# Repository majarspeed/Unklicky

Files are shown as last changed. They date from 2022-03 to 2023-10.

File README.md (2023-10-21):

# Thank you Guys 
I love seeing the makes and all the questions and some awesome derivates are coming out of this project. 

And there is an amazing Euclid derivitive doen by Minisekt you can view [Unclid here](https://github.com/Minsekt/unclid).

There are new versions of the unklicky for the KlickyNG, JosAr has integrated the unklicky concept into the NG or next generations of Klicky. Check it out here https://github.com/jlas1/Klicky-Probe/tree/main/Probes

A great tutorial on Klicky/Unklicky was made by a member of the discord if you have any questions this should help for the setup. Thanks Logan BC 🇨🇦 VT.435 for creating such a great resouce. https://github.com/LoganFraser/VoronMods/tree/main/KlickySetup

# Unklicky

Drop in magnet based klicky probe In the orginal and now a 6x3 magnet variant called the BFP. 

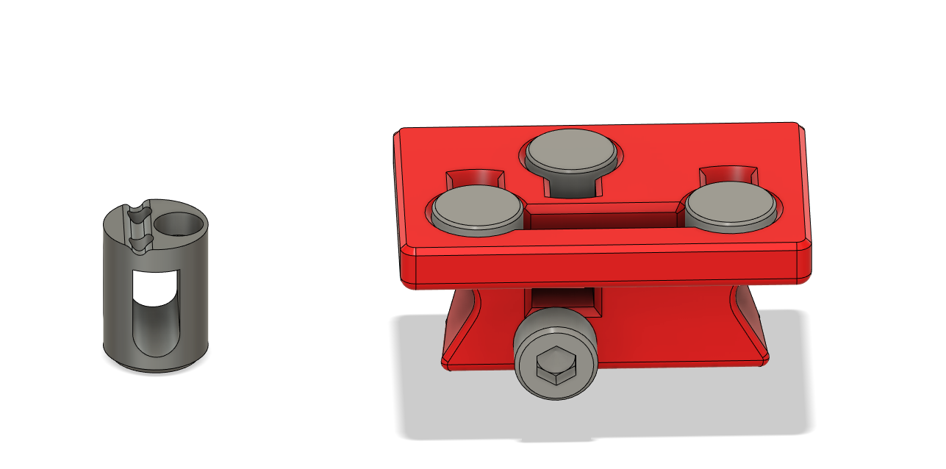
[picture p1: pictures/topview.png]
Top

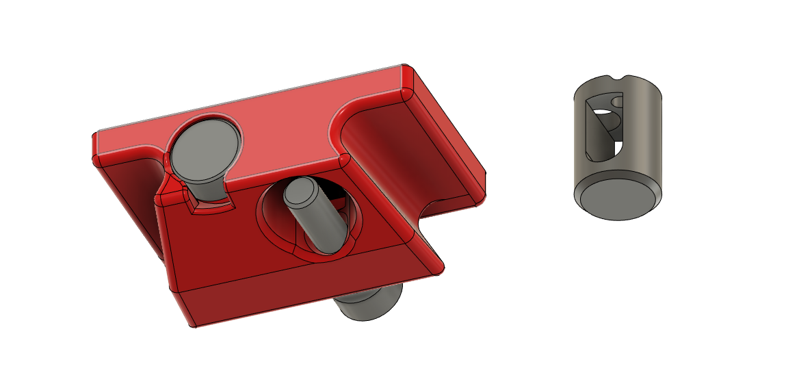
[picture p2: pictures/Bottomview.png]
Botton Bottom


Also keep in mind that klicky is based off the original work done over at Annex Engineering the excellent work that was done with the quickdraw probe. 
Thanks for calling this out. I did know the original was based on their work but it slipped my mind. They have an excellent group that does a lot of good things for the community. Support them in there work and thanks for keeping me honest here guys. 
https://github.com/Annex-Engineering/Quickdraw_Probe

Klicky is also based on [Euclid](https://www.euclidprobe.com/).

Thanks go to JosAR again for all the hard work and testing, please support his project and all the hard work he has done and is continuing to do. 
https://github.com/jlas1/Klicky-Probe

Testing with the auto z
While the switch offset can be changed by wire thickness on the wrap. 6mm seems to be a safe starting point for the the unklicky. And 3.2 seems to be a good starting point for the BFP. You can mesure from the body to the probe point to get the switch offset. And visit Protoloft and support him for all the work he has done on the auto z project. https://github.com/protoloft/klipper_z_calibration 

Parts kits thanks to DFH

[Buy full kit here](https://deepfriedhero.in/products/unklicky-full-kit-by-dustinspeed?_pos=1&_psq=unkl&_ss=e&_v=1.0&aff=8 "Full Unklicky Kit")

[Buy sidegrade kit here](https://deepfriedhero.in/products/unklicky-sidegrade-kit-by-dustinspeed?_pos=2&_sid=d0a66cc6e&_ss=r&aff=8 "Sidegrade Unklicky Kit")

# Unklicky TAP

This is a unklicky sensor for TAP. Thanks to the Voron team for this design and Badnoob for spearheading the effort and lead developer role.

It's almost as precise as the optical sensor, it's main goal is to reduce the initial Voron hug (a lot of people start buying the same obscure part, leaving it out of stock). With that said i can see one using it as a primary sensor as it can achieve a range in probing better than 0.0025 with a standard deviation of 0.001.

**A range of 0.001 is excellent and enough for our 3D printer needs.** don't chase unicorns.

It's pretty easy to install, it does require a somewhat tuned printer.

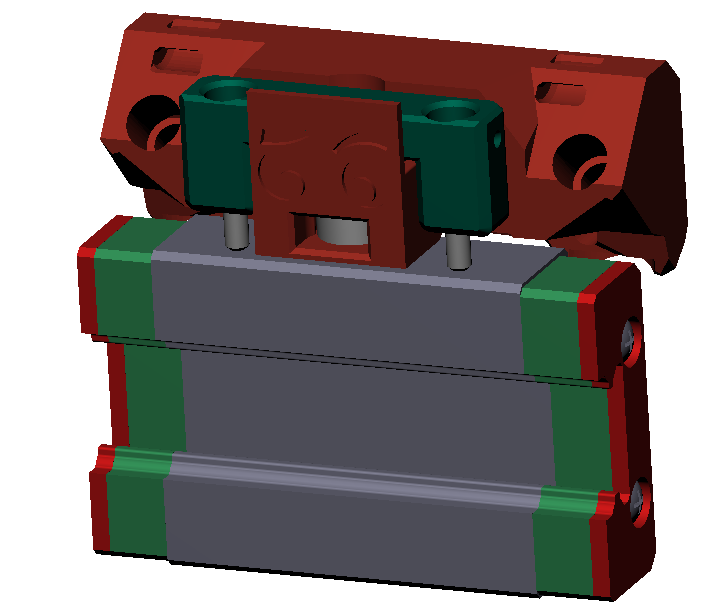
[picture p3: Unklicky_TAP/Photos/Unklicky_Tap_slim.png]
Unklicky TAP
|  |
| :----------------------------------------------------------: |

# How does it work?

The principle behind this sensor, is using the MGN12 steel carriage to make contact with two m2x10 self tapping screws, thereby closing the circuit between the mcu GND (or V-) and the probe (should use a endstop) signal pin.
Two 6x3 magnets makes the pin attract the probe body.

## More information

More information [here](./Unklicky_TAP)

## Versions and differences 

| Unklicky TAP | usage |
| --- | --- |
| ~~Unklicky TAP~~ | ~~It's almost a drop in replacement/spare for the optical PCB for TAP, it uses the same footprint, is installed on the same TAP upper part, but only requires 2 cables, a mcu GND (or V-) and the probe (should use a endstop) signal pin, it does not need a 5v connection.<br />Requires Umbilical cables to the toolhead~~<br />Discontinued, the released TAP upper part is too large, screws don't touch on the MGN12 carriage |
| [Unklicky TAP](./Unklicky_TAP) | It's embedded in it's own TAP upper part (due to space constrains between TAP and the cable chains), but only requires 2 cables, a mcu GND (or V-) and the probe (should use a endstop) signal pin, it does not need a 5v or 24v connection.<br />Previously called UnklickyTAP slim, renamed when the larger sibling was discontinued |

| Unklicky Probes | usage |
| --- | --- |
| [Unklicky](./Unklicky_Probes/Unklicky) | The original. Made to retain the same shape and body as klicky. It uses 3x2 magnets in the pin. Uses wire wrapped pin method |
| [Unklicky BFP](./Unklicky_Probes/BFP) | Larger body to allow the use of a 6 x 3 standard magnet. Uses the original wire wrapped pin method |
| [Unklicky BFP-HS](./Unklicky_Probes/BFP-HS) | Even Larger body to allow the use of a 6 x 3 standard magnet and a heatset in the pin to allow a shorter pin throw. And more clearance for wires. Does not increase accuracy but does make the build easier. |
| [Unklicky BFP for v0/Tiny-M](https://github.com/jlas1/Klicky-Probe/tree/main/Probes/Unklicky) | Larger body to allow the use of a 6 x 3 standard magnet, pivot arm version to reduce inaccessible bed space. Uses the original wire wrapped pin method |
| [UnklickyNG](https://github.com/jlas1/Klicky-Probe/tree/main/Probes/UnklickyNG) | Original Unklicky mod compatible with [KlickyNG](https://github.com/jlas1/Klicky-Probe/tree/main/Probes#klickyng) mounts. It uses 3x2 magnets in the pin. Uses wire wrapped pin method |
| [UnklickyNG BFP](https://github.com/jlas1/Klicky-Probe/tree/main/Probes/UnklickyNG) | Original Unklicky BFP mod compatible with [KlickyNG](https://github.com/jlas1/Klicky-Probe/tree/main/Probes#klickyng) mounts. Larger body to allow the use of a 6 x 3 standard magnet. Uses the original wire wrapped pin method |
| [Unclid](https://github.com/Minsekt/unclid) | Unclid Probe ([Euclid](https://www.euclidprobe.com/) probe replacement), uses two screws and the magnet to close the switch circuit |
| [Sidewipe Unklicky](https://github.com/chestwood96/SlideSwipe/tree/master/Experimental/UnklickySlideSwipe(better%20name%20pending)) | Sidewipe Unklicky by chestwood96, This is a bit of a mixture of unklicky and mechabl in a SlideswipeProbe formfactor.  |

| Unklicky Endstops | usage |
| --- | --- |
| [Unklicky Z](./Unklicky_Endstops/Unklicky_z) | First standard z endstop has multiple pin options. Uses the Heat set pin method and was intended to be modular and allow for customization of the pins |
| [Unklicky Sexbolt](./Unklicky_Endstops/Unklicky_SexBolt) | Sex bolt mod. Uses a single pin and 5mm OD chicago screw or sexbolt and 695/f695 bearing. |
| [Unklicky Sexbolt-SBS (bearing sleeve)](./Unklicky_Endstops/Unklicky_SexBolt) | Sex bolt mod. Uses a single pin and 5mm OD chicago screw or sexbolt. Allows the reuse of bearing sleeve from other sexbolt mods. |
| [Unklicky Sexbolt Bearing free version](./Unklicky_Endstops/Unklicky_SexBolt) | Sex bolt mod. Uses a single pin and 6mm OD and 5mm rod with a chicago screw or sexbolt. |
| [Parametric Sexbolt unklicky Z](https://github.com/PorcoMaster/SexPillar) | Parametric Sex bolt + Unklicky mod. (from PorcoMaster) |

| Other Unklicky inspired designs | usage |
| --- | --- |
| [RunoutUnklicky](https://github.com/waytotheweb/voron/tree/main/general/RunoutUnklicky) | The Runout UnKlicky Sensor is a filament runout sensor that can be used to pause a print if printing filament breaks, runs out or otherwise is no longer present in the sensor.The design uses magnets as the switch, making it easy and cheap to source BOM components. |

# Unklicky Newest version 2
New version of the 3x2 probe is now available. This includes some QOL improvements. But does not really improve on any performance in any significant way. 
Added a screw mount on the rear so a magnet or screw can be used. May be useful if you have especially strong magnets.
Added a shaped pin that is easier to wire. And only inserts in one direction. 
New pin can be printed flat on the plate to make it easier to print and align the layer lines for smoother operation. 
V1 will be retained for now as well.

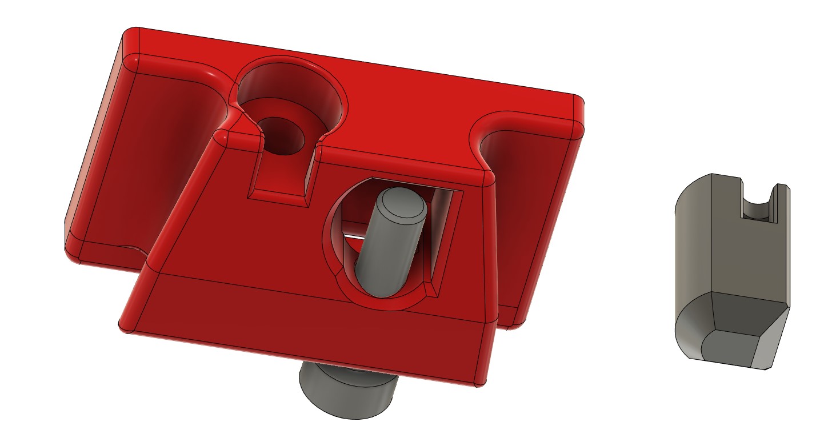
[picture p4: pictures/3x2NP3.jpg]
V2 3x2


# BFP newest Version 6

This is a 6x3 unklicky probe, it's a mod developed by me and JosAr.
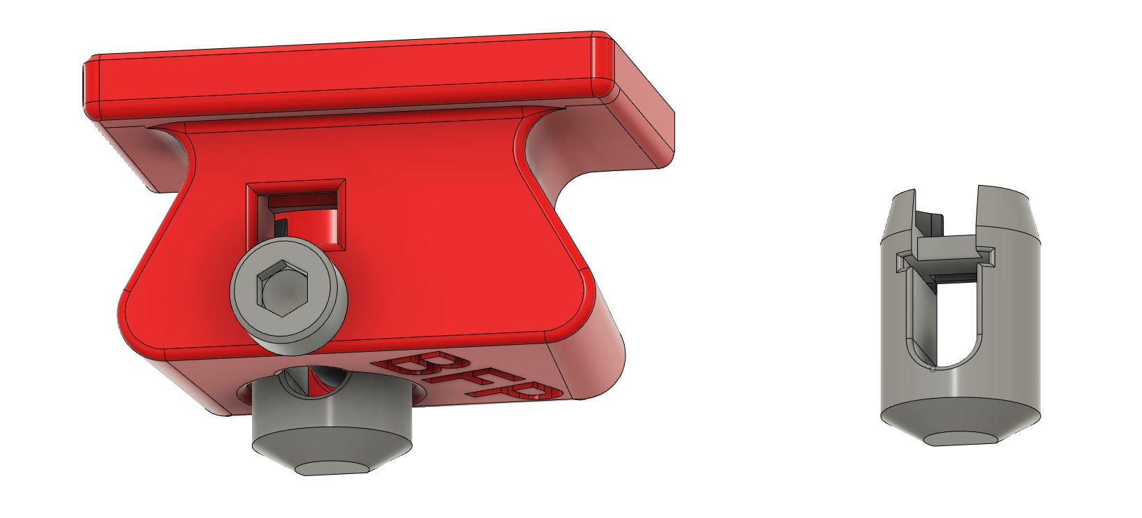
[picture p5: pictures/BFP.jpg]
bfp BFP


With the D-shaped shaft make sure there is no elephant foot to interfere with the motion. 
we have found for the wire to to the PIN/stalk it does seem to work better with a bare wire. 
Please feel free to reach out if you have any issues. 

# But how does it work!! 
There has been a lot of questions around this. So hopefully I can shed some light. 
The Probe uses an internal magnet on top of the pin/stalk. This magnet is not part of the circuit it is only used to provide a spring for the the probe. 

The real part of the probing is actually done by the screw. 
There is a contact point between the screw and the wire. This allows the unklicky to be normally closed. 
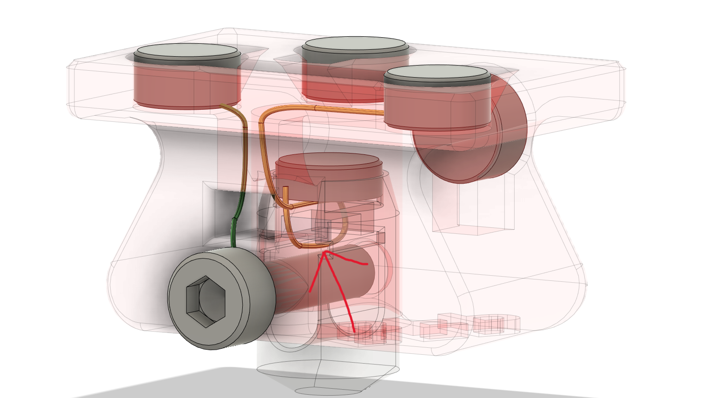
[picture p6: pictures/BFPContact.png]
Contact

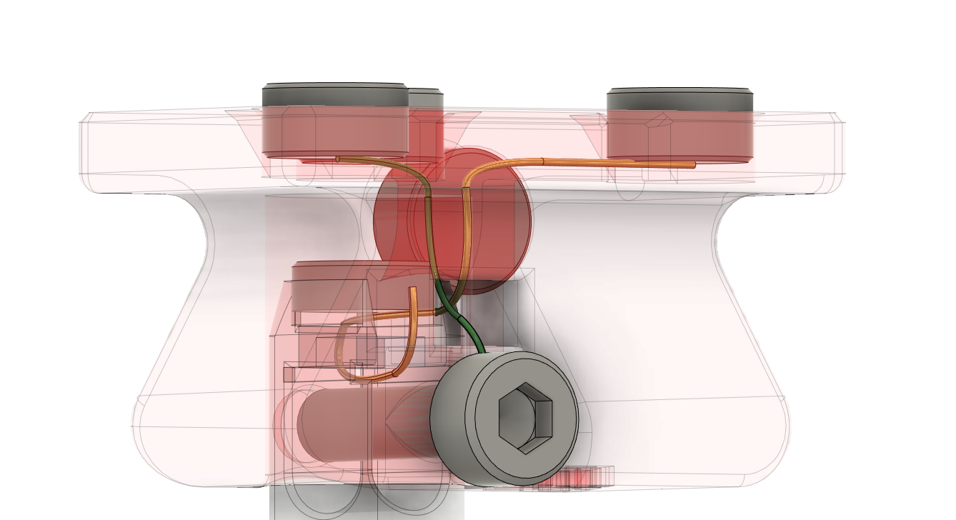
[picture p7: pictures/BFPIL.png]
Left


# But how well does it work!! 

Measurements were at 240 hotend, 95 bed, 55 chamber, on a Z belted [Tiny-M](https://github.com/gsl12/Tiny-M).
10k probe accuracy tests with 5 touches each. 
In the sense distance you can see the heatup at the start. And the consistency once up to temp.
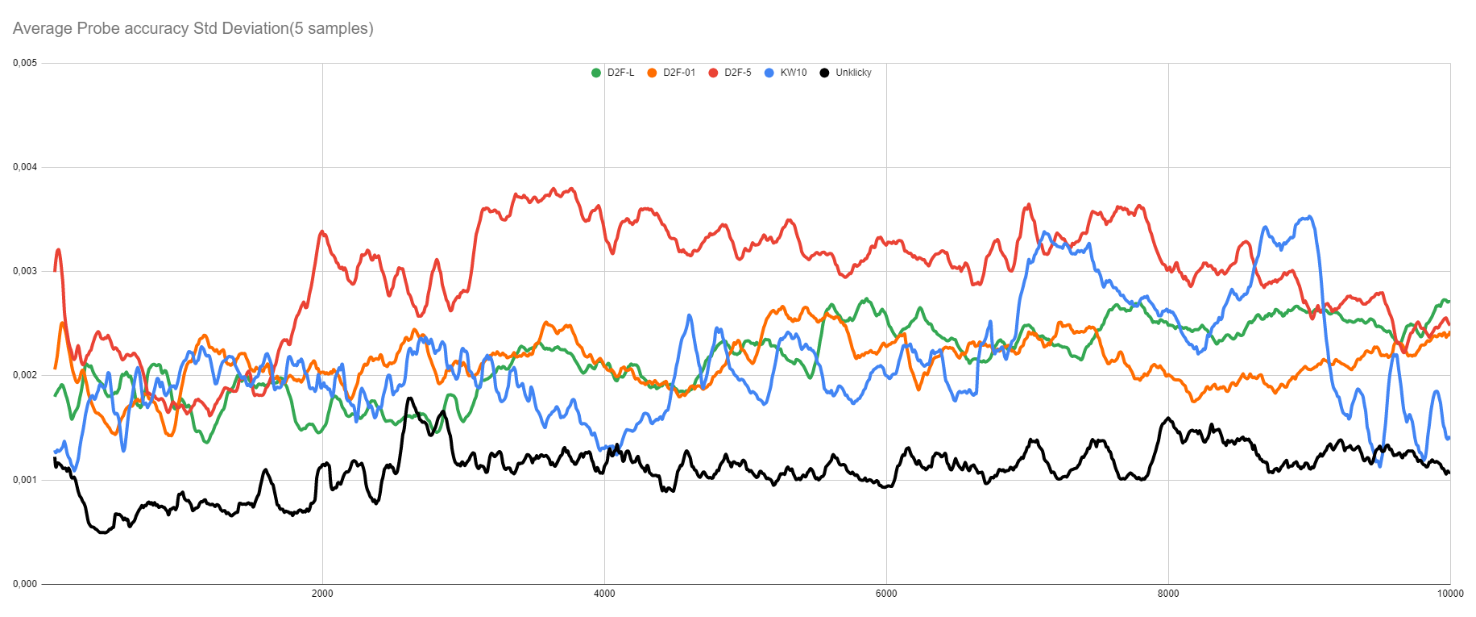
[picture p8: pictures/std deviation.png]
Deviation


Besides being one of the most precise switch's of the microswitch shootout (which will have soon a dedicated repository by JosAr), it withstood 50000 probes at 3mm/s

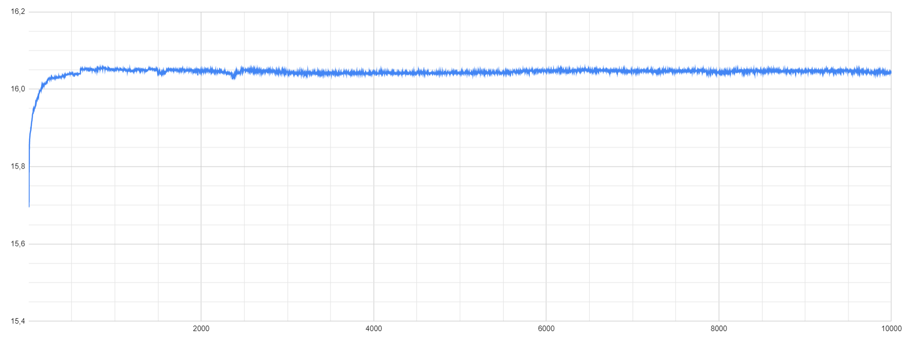
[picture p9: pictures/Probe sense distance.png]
sense distance


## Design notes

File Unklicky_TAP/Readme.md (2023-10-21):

# Unklicky TAP (unTAP)

This is a unklicky sensor for TAP. Thanks to the Voron team for this design and Badnoob for spearheading the effort and lead developer role.

It's almost as precise as the optical sensor, it's main goal is to reduce the initial Voron hug (a lot of people start buying the same obscure part, leaving it out of stock). With that said i can see one using it as a primary sensor as it can achieve a range in probing better than 0.003125 with a standard deviation of 0.000841.

**A range of 0.005 is excellent and enough for our 3D printer needs.** don't chase unicorns.

It's pretty easy to install, it does require a somewhat tuned printer.

This version, due to size requirements (needs to fit between TAP and X cable chains), it needs to replace TAP upper parts.

This is functionally  a drop in replacement/spare for the optical PCB for TAP, it uses it's own TAP upper part, but only requires 2 cables, a mcu GND (or V-) and the probe (should use a endstop) signal pin, it does not need a 5v or 24v connection.

| Unklicky TAP |
| :---------------------------------------------: |

# How does it work?

The principle behind this sensor, is using the MGN12 steel carriage to make contact with two m2x10 self tapping screws, thereby closing the circuit between the mcu GND (or V-) and the probe (should use a endstop) signal pin.
Two 6x3 magnets makes the pin attract the probe body.

On the image bellow, you can see Unklicky TAP sensor touching the X axis MGN12 carriage.

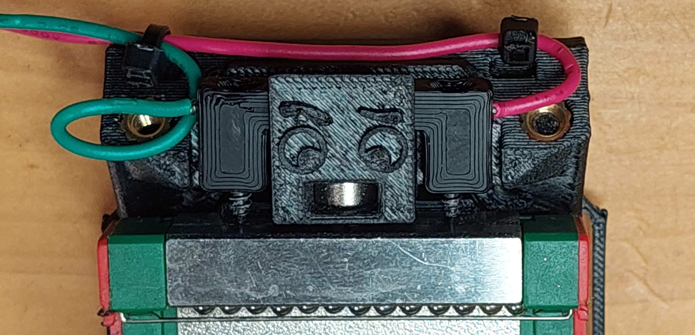
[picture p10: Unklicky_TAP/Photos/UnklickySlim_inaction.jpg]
Unklicky TAP
|  |
| --------------------------------------------------- |

More instructions below:

# What do I need?

## Bom
| Name | Pieces |
| --- | --- |
| M3 Heatset insert | 4 |
| 6x3mm Magnet | 2 |
|M2x10 self tapping screw| 2 |
|18 to 22 AWG wire| as required |

## Printed parts

| Name | Pieces |
| --- | --- |
| UnTAP_Body_v2.stl | 1|
|UnTAP_pins_v2| all |

There are more pins that may suit your printer better, see if any helps you on your issue (the 9mm pin for instance allow a 9mm screw to reach the carriage, a 10mm screw would go 1mm deeper into the MGN12 carriage.

The V2 version compared to the v1 is longer, so the screws are in a better location (some Carriages have a slot in the middle that can disturb the probing).

I recommend to print all the pins, they are really fast to print and it's a lot easier to print them at once.

### Printing instructions

The parts should be printed with the definitions below, they are oriented ready to print:

* initial layer height:0,24
* layer height: 0.2mm
* bottom/top/perimeters: 4
* infill: more than 30%
* infill type: Cubic
* Thin walls: On

The TAP Body requires supports, but they are included in the model.

## Build

| Instruction | Image |
| --- | --- |
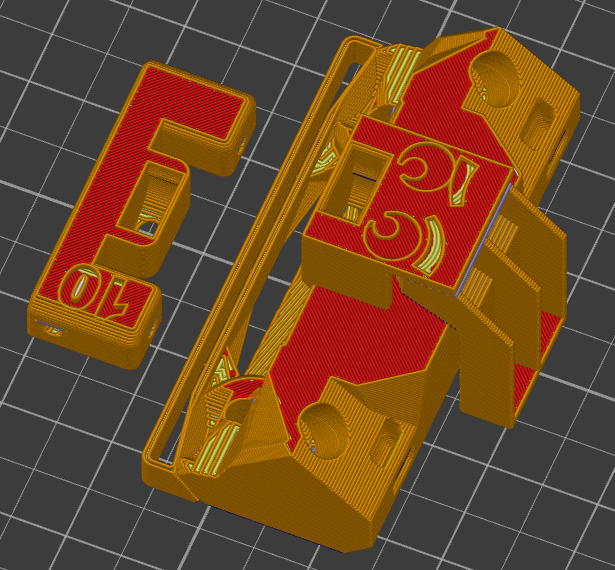
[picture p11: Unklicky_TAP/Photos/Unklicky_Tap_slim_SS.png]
Instructions
|1. Print the parts as they are oriented and remove the body support.|  |
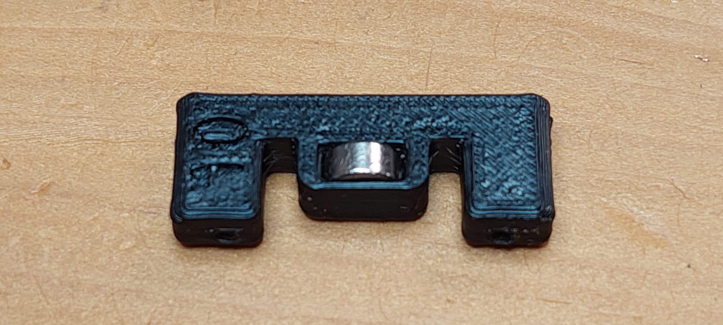
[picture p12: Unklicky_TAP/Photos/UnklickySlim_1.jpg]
pin magnet Pin magnet
|2. Insert the pin magnet, it should be insert until the it can no longer move. A small part of the magnet will remain outside the slot.|  |
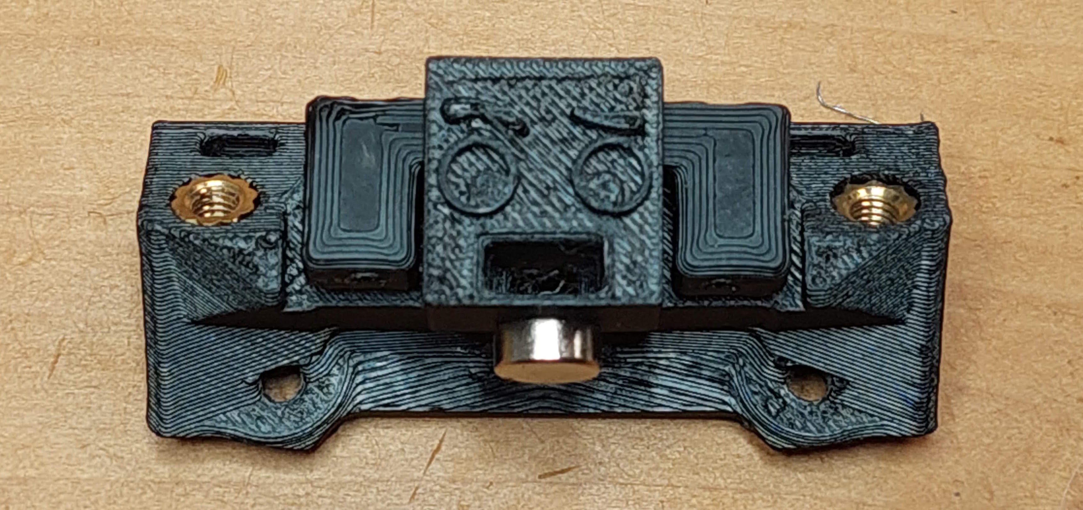
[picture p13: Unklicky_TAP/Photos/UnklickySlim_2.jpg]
body magnet orientation
| 3. Rotate the pin and place it on the sensor body, with the magnet opening facing the back.<br />The pin magnet opening is facing the back in the image<br />Attach the other magnet to the outside of the body, and make sure that you respect that orientation when it is inserted on the probe body, both magnets should attract. ||
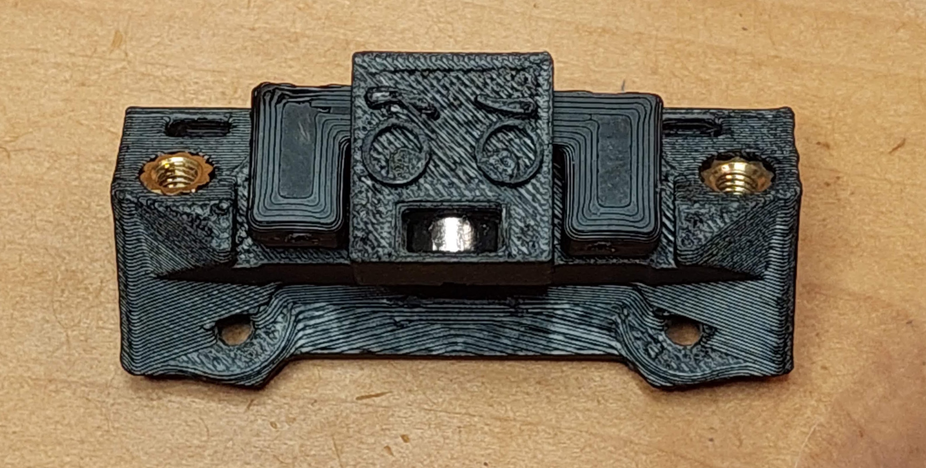
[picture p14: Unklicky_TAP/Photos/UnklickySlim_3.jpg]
body magnet
|4. respecting the polarity, insert the magnet in the sensor body, it should go all the way in, with a bit of force, then stay there. (the groove that holds the magnet was actually designed by Badnoob)<br />Verify that the pin moves freely and jumps back to its resting position reliably. If the pin sticks or jams, try lightly sanding the top and bottom layers.||
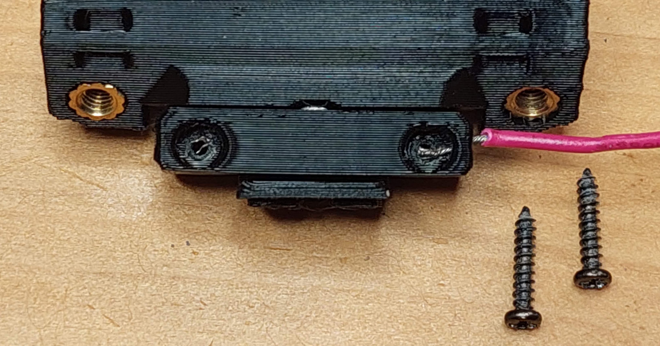
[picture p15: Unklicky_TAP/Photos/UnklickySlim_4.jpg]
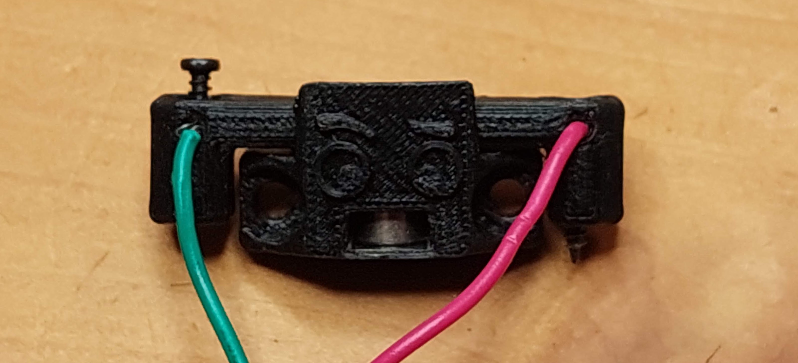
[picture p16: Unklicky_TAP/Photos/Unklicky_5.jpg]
|5. Slot one of the wires trough the side holes, screw a m2x10 self tapping screw on the hole, making sure it is solidly installed.<br />Repeat this procedure for the other side of the pin.| <br /> |
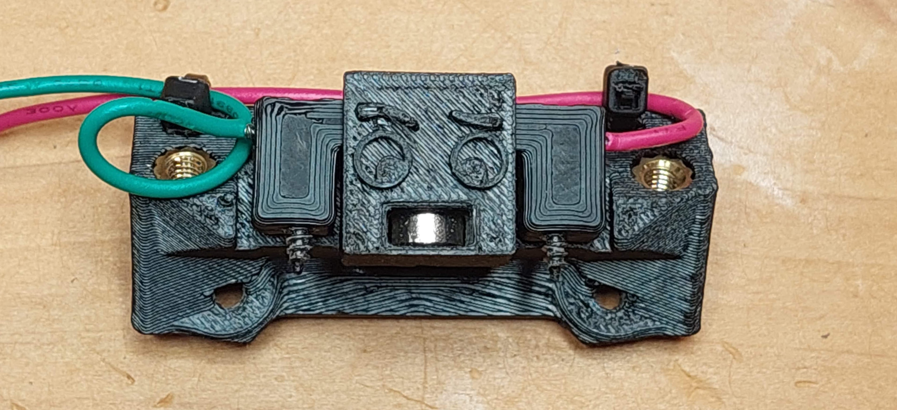
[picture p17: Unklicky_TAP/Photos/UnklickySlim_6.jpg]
final look Final look
|6. the sensor is now ready to attach to TAP as it's upper body instead of the Optical PCB sensor + TAP upper part, you can use zip ties to secure both ends of the connectors, just leave room for the pin to move up and down.|  |

## Klipper configuration

Below are the klipper specific unklicky TAP probe configuration, for the rest, please follow the TAP optical probe manual and procedures, they are the same.

```jinja2
[probe]
pin: ^Pin [should enable pullups "^" and use a endstop pin for better effect]
speed: 5
sample_retract_dist: 1.0
samples_tolerance: 0.05
samples_tolerance_retries: 3
```

## Initial run

After initial assembly, don't forget to check your Z probe offset, it will have changed.
**You should also condition the probe with the Klipper command "probe_accuracy samples=5000"** somewhere on top of the bed, it helps getting better results faster.
Speaking of faster, the best results for UnklickyTAP is between 5 and 10mm/s probe speed.

if you decide to use it, give me feedback, either here, or on Voron discord, my discord user is JosAr#0517, feel free to ping me in this channel  [Usermod probes help](https://discord.com/channels/460117602945990666/969563854071799818)

Please feel free to reach out if you have any issues.

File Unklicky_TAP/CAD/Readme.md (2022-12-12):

V6: pushed the pins more to the back of the carriage, to move away from the ridge that some carriages have

v7: extended the pins to allow an easier sanding on the surfaces that touch the body

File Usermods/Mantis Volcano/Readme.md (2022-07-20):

This is unklicky probe for Mantis and Volcano hotend.

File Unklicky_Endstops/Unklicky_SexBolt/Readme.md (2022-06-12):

# Unklicky Sexbolt

This is a 6x3 unklicky Z end stop . 

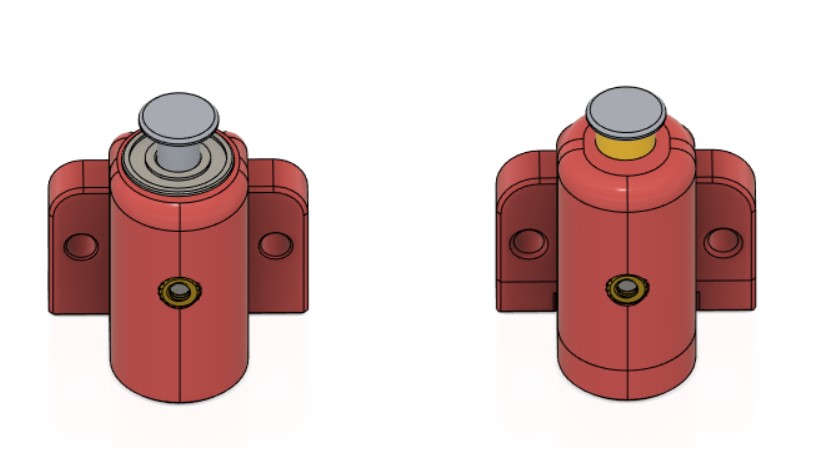
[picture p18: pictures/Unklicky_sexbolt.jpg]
SexBolt Instructions


## Bom
| Name | Pieces |
| --- | --- |
| 6x3MM Magnet | 2|
|18 mm M3 screw| 1|
|18 to 22 AWG wire| <100 mm does not include wire to the board|
|Microfit 2 wire Male connector| 1|
|Microfit 2 wire Female connector| 1|
|Microfit 2 wire Male pins| 2|
|Microfit 2 wire Female Pins| 2|
|M3 heatset inserts| 3|
|M3 6 mm screws| 2|
|M4 threaded rod 10mm| 1 can use a m4 screw with the head removed|
|Optional for no bearing version M5 threaded rod 10mm| 1 can use a m5 screw with the head removed|
|M5 bearing sleeve or 695 flanged or unflanged / bearing| 1|
|M5 sexbolt/Chicago screw 12 mm for standard height 20mm for kinematic| 1| 
|Optional for no bearing version M6 sexbolt/Chicago screw 12 mm for standard height 20mm for kinematic| 1| 

## Printed parts Bearing
| Name | Pieces |
| --- | --- |
| Unklicky_SB_Body.stl | 1|
| Unklicky_SB_pin.stl| 1|

## Printed parts For bearin sleeve
| Name | Pieces |
| --- | --- |
| Unklicky_SBS_Body.stl | 1|
| Unklicky_SBS_bottom.stl | 1|
| Unklicky_SB_pin.stl| 1|

## Printed parts bearing free version
| Name | Pieces |
| --- | --- |
| Unklicky_SB_Body_6mm.stl | 1|
| Unklicky_SB_bottom_6mm.stl | 1|
| Unklicky_SB_pin_6mm.stl| 1|

## Build
| Instruction | Image |
| --- | --- |
|1. Ensure the pin and body slide together very well. Sand or clean up any parts that do not slide well. And that a screw in the pin slot can slide up and down correctly.| |  
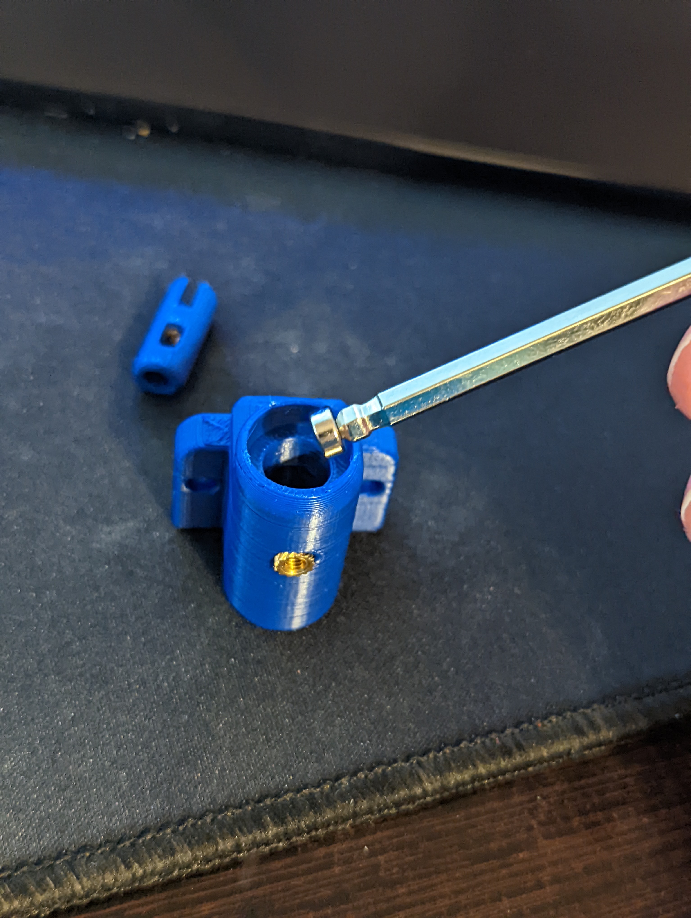
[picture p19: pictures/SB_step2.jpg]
|2. Insert bottom magnet. For the Bearing version use a large hex wrench to reach the bottom and slot the magnet into place. On the sleeve version it is on the bottom part.  | |
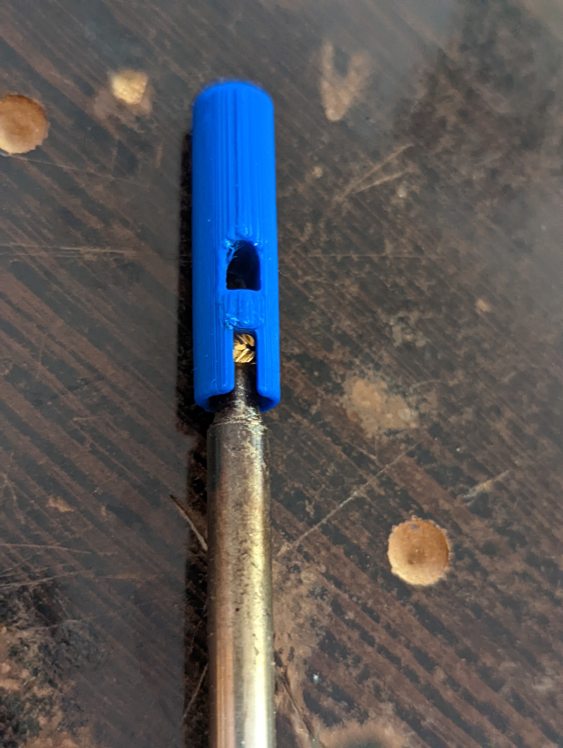
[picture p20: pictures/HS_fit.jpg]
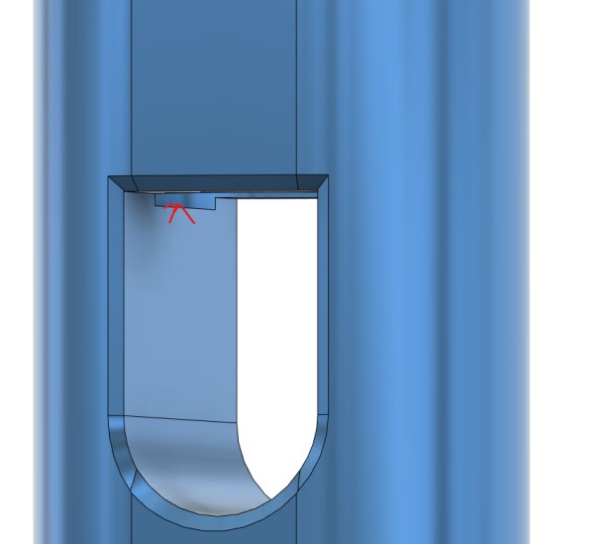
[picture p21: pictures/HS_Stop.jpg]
|3. Use a iron to press the heat set into the end of the pin. Being very careful to stay away from the mag retaining walls. There is a bump added to the model I can feel the heat set when it hits these stops but it possible to push past these stops. So you want a almost hairline amount of heat set showing in the screw slot. Also since we are pressing this through plastic use a pick or file to ensure the bottom of the heat set is clear of plastic to make a good connection.||
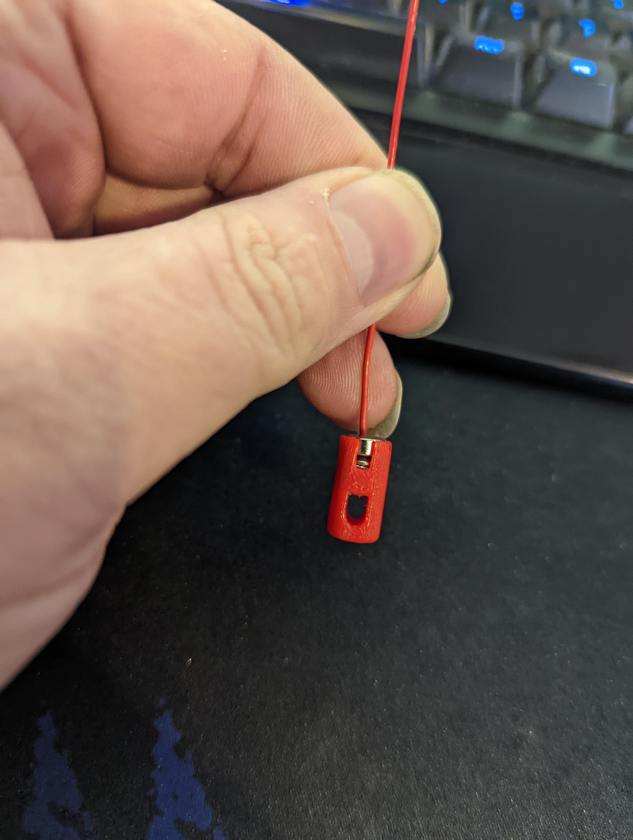
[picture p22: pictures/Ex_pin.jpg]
|4. Strip and wrap the wire around the m3 screw with sticking out on the D-cut side of the pin.||
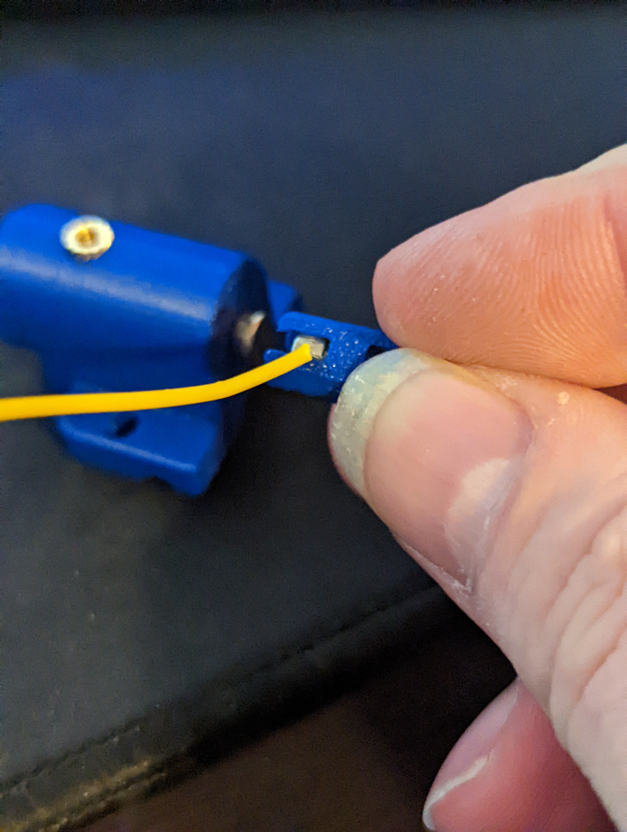
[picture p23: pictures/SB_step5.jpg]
|5. Place a magnet on outside of the body of the installed bottom magnet. And use that to insert the pin mag into the pin. This magnet will be pushed not pulled. So it is not critical to be super secure. For that reason the fit is fairly loose and you may need to slide it off the top. This is by design to prevent any swelling in the pin that can cause roughness in the pin sliding.||
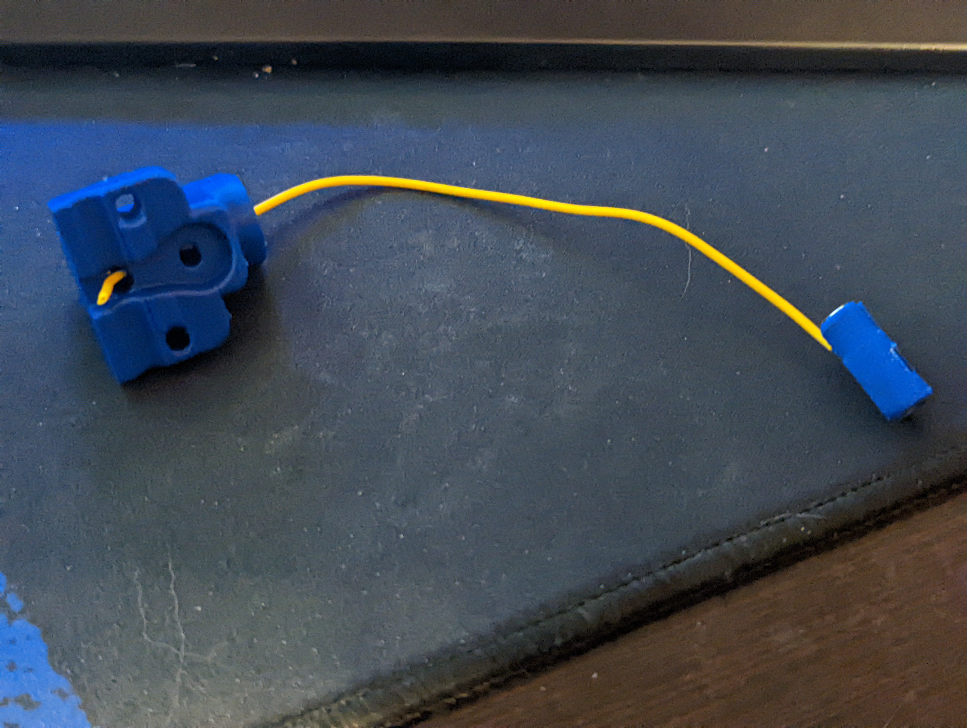
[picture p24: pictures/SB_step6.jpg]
|6. Slot the other end of the wire for the pin through the bottom rear hole.|![Instructions] |
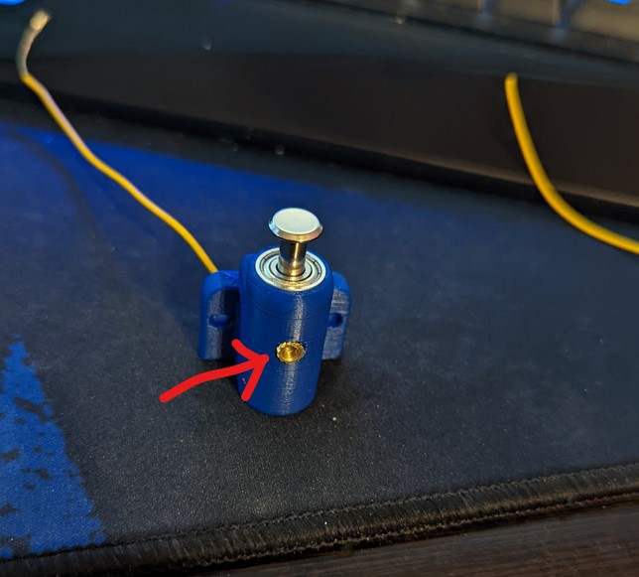
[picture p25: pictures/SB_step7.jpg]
|7. Press a heat set in the front of the body. |
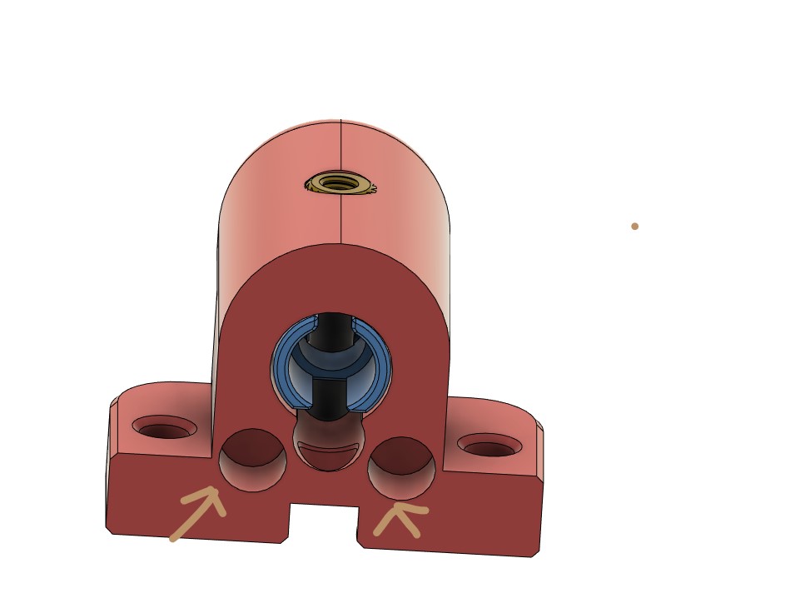
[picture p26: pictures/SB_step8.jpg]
|8. Press 2 heat sets in the bottom of the body if using the sleeve version.| |
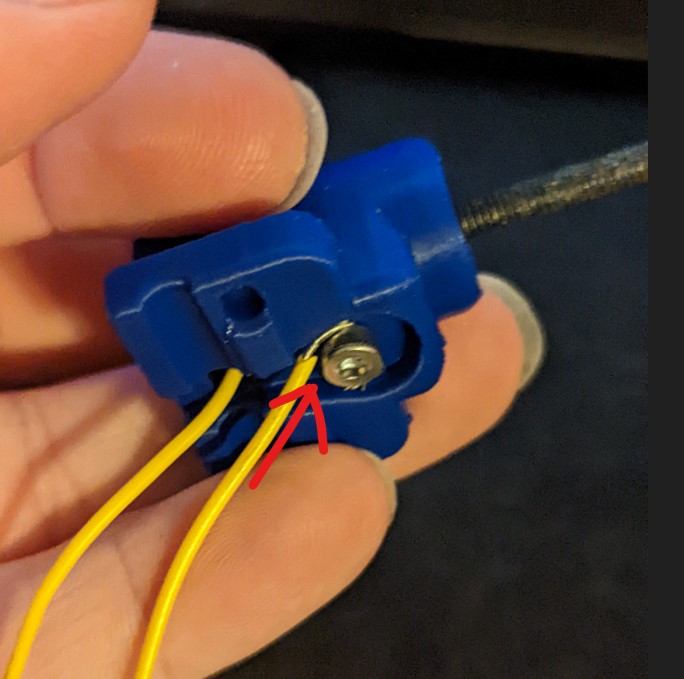
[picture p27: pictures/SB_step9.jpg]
|9. Wrap the second wire around the contact screw. Screw the contact screw into place from the rear. Ensure that the pin is pushed in and aligned correctly. And that the pin is sliding as expected.| |
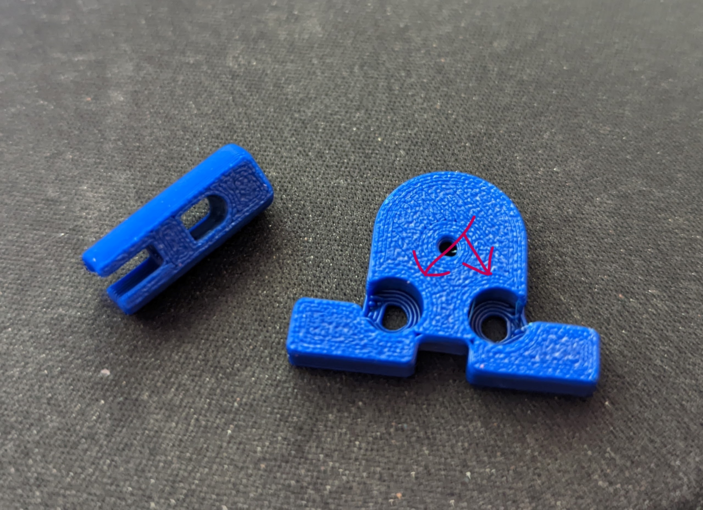
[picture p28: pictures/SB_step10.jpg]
|10. If using the sleeve version use 2 m3X6 mm screws to attach the bottom to the body.| | 
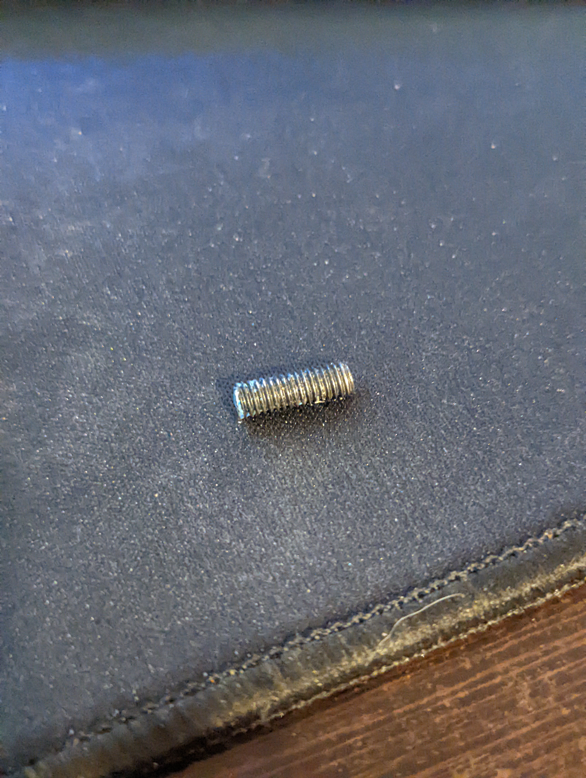
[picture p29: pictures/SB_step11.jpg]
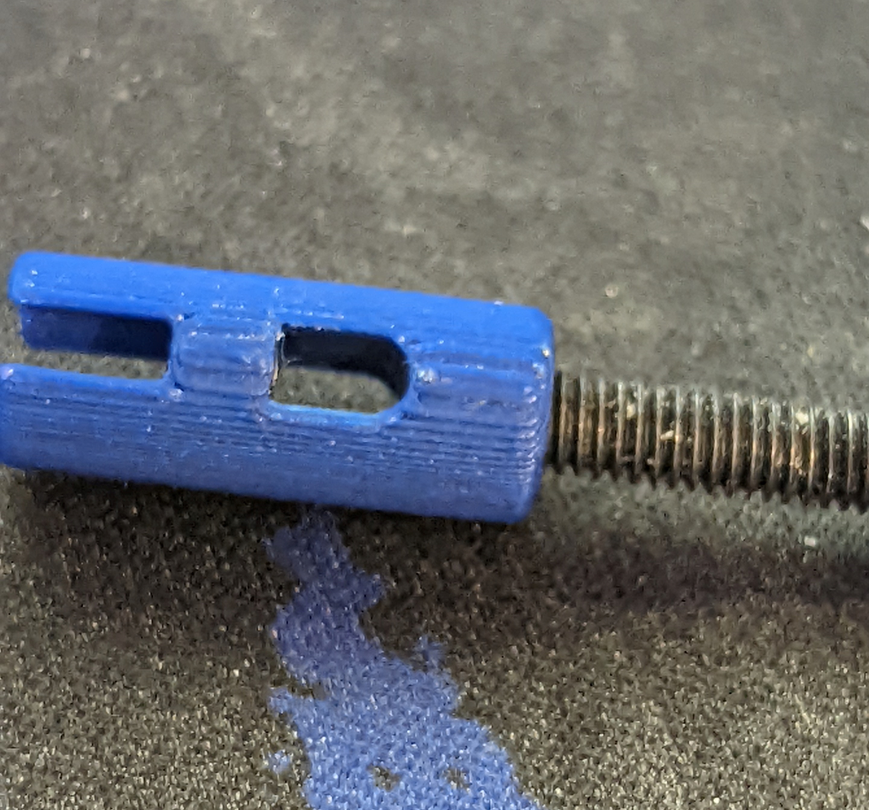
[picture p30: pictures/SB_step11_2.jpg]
|11. thread the m4 rod into the end of the pin.|  |
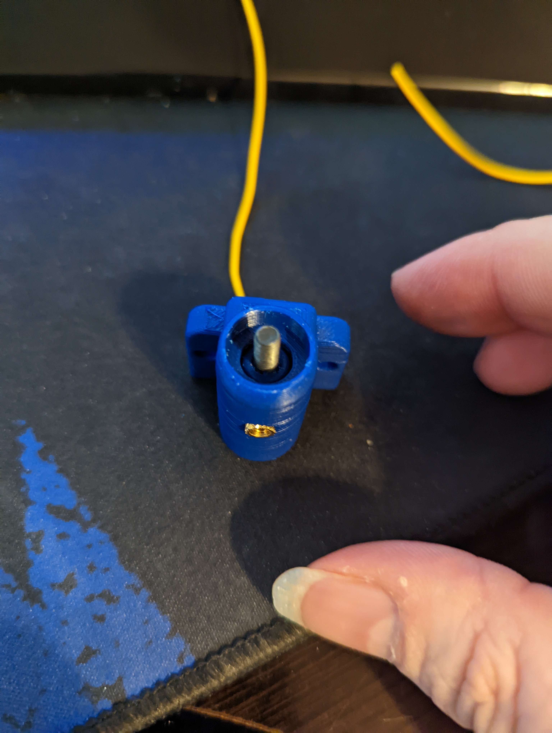
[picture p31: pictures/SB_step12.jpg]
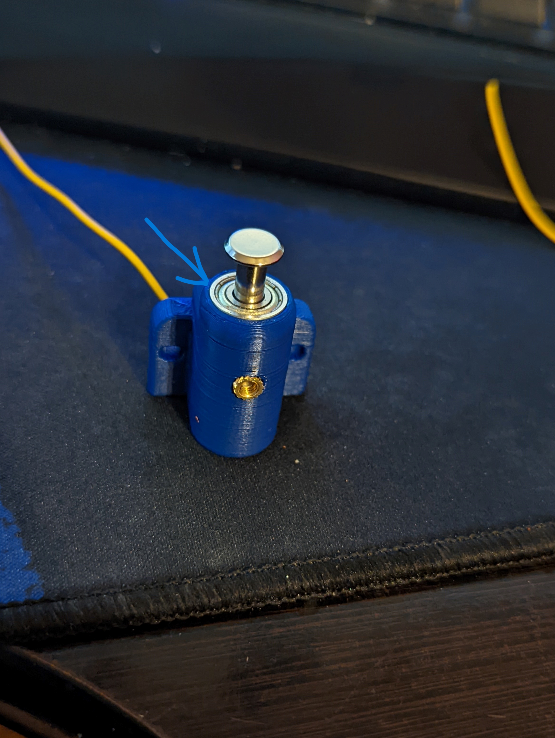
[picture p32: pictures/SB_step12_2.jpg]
|12. Press the sleeve or bearing firmly into the top of the body. And screw the SexBolt onto the m4 rod.|   |
|13. Crimp the wires from the sex bolt and from the board with the microfit connectors.| |
|14. Screw the sex bolt body to the extrusions using 2 m3 x 8 screws. This does assume that you use the existing end stop hardware.| SexBolt Instructions |

If you run into issues I am available on the voron discord most times. Feel free to ping me in this channel.  [Help I broke my klicky](https://discord.com/channels/460117602945990666/969563854071799818). Discord name Dustinspeed#6423. 

Please feel free to reach out if you have any issues.

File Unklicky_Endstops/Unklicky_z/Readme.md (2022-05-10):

# Unklicky z V3 
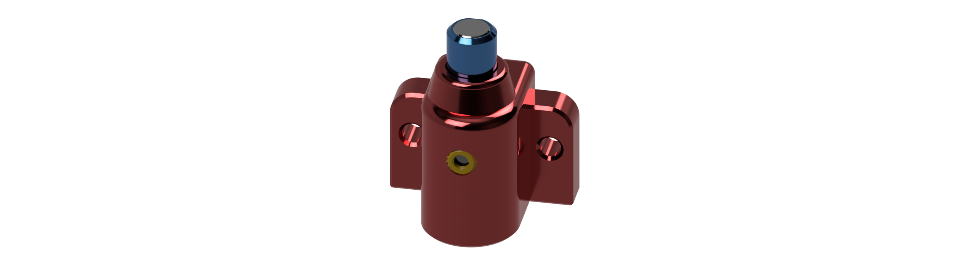
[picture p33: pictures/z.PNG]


# Updates and additions 

V4 body added addtional wire path. Increased the rear screw clearance. And made the locating tabs 6mm. 

Added a 5mm pin for using a 5mm steel pin.

Added a 4mm threaded pin for use with a 4 mm carriage bolt or hexbolt. 
Printed the one I tested at .15 layer height. should be fine at .2. 

You can use a sex bolt with the unklicky z. you need a 4 mm threaded rod or cut the head off of a 4mm screw and use that as a post into the 4mm threaded pin. 

I have added some generic pins. To the cad that are intended to be building platforms. If you have a good Idea for a pin let's see it @@ 

# V3 major change
z3

Moved the bottom magnet inside the body to allow it to be closer to provide more lift. 
Changed the contact to not require a wire wrap. Now the heatset will contact to the contact screw directly. 
Wire is securured under the screw now to make a cleaner method of securing. 
There is a slot to stop the heatset you will feel it bump when it is deep enough.
The new magnet locations have increased the spring to around a 245 grams of lifiting force. (this is using my finger and a scale take with a grain of salt) But this is about 150% increase from the v1.

There has been a script created to test the noozle ooze that can be used for any probes and endstops.  But do want to thank Jkwang for a great new tool. You can grab it from his github at https://github.com/johnnykwwang/3dp_notes/tree/main/auto_z_accuracy_test. 

Initial test results. 

Switch 50 probes
// probe accuracy results: maximum -0.238438, minimum -0.267500, range 0.029063, average -0.259494, median -0.260313, standard deviation 0.004410

Unklicky z 50 Probes 
// probe accuracy results: maximum -0.069688, minimum -0.072188, range 0.002500, average -0.070969, median -0.070938, standard deviation 0.000542 

// probe accuracy results: maximum -4.640313, minimum -4.641563, range 0.001250, average -4.640656, median -4.640625, standard deviation 0.000381

// probe accuracy results: maximum -4.658438, minimum -4.659688, range 0.001250, average -4.659031, median -4.659063, standard deviation 0.000406

// probe accuracy results: maximum -4.638750, minimum -4.640000, range 0.001250, average -4.639250, median -4.639063, standard deviation 0.000468

z3
z3
z3
z3

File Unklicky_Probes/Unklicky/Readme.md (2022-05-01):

# Unklicky

Drop in magnet based klicky probe. 

Top
Botton Bottom

# What do I need?

## Bom
| Name | Pieces |
| --- | --- |
| 6x3MM Magnet | 4|
| 3x2mm Magnet | 1|
|12 M3 screw| 1|
|18 to 22 AWG wire| <100 mm|

## Printed parts
| Name | Pieces |
| --- | --- |
|Unklicky_Shapedpin_body_v2.stl | 1|
|Shapedpin_point_v2.stl| 1|

## Build
| Instruction | Image |
| --- | --- |
|1. Ensure the pin and body slide together very well. Sand or clean up any parts that do not slide well. And that a screw in the pin slot can slide up and down correctly.| |  
|2. Insert rear top magnet. Note: needs to be aligned to attract to dock magnet if existing mount is in place. Or if this is a new installation will need to be reversed alignment from the front 2 slots we will do later.| Instructions|
|3. Strip and wrap the wire around the pin with the starting point being on the D-cut side of the pin. Multiple wraps around the pin can be used for thinner wires. But you want to be careful to have it flat on the bottom. And use a single twist and cut any extra off on the side as wire binding will cause the pin to not move smoothly.|Instructions Instructions|
|4. Place a magnet on top of the installed rear magnet. And use that to insert the pin mag into the pin. This magnet will be pushed not pulled. So it is not critical to be super secure. For that reason the fit is fairly loose and you may need to slide it off the top. This is by design to prevent any swelling in the pin that can cause roughness in the pin sliding.|Instructions|
|5. Slot the other end of the wire for the pin through the body to the top of the body. Note: in the newer body this will be easier to see and slot. But it is very similar to threading a needle.  Cut and strip the wire on on top with the stripped end going under either magnet.| NOTE: In the image I am showing the path to thread the wire through the part. Instructions|
|6. Slot a new wire for the contact screw strip a small portion of wire. This can either be stuck into the hole and insert the wire or wrap the wire around the screw. On top strip the other side of wire and place under the other front magnet.| NOTE: In the image I am showing the path to thread the wire through the part. Instructions Instructions|
|7. Screw the contact screw into place. Ensure that the pin is pushed in and aligned correctly. And that the pin is sliding as expected.| Instructions|
|8. Change the z height for Probe and QGL/z-tilt to a move height of 25 mm. This should work for any of the unklicky probes.| |
|9. While I am not going to go into auto z here. The unklicky currently can start with a switch offset of 6 mm and BFP 3 mm. These should set you a touch high and can be adjusted down. The main variability here is the wire wrap height. But this should be safe for almost anybody. PLEASE test I do not want to see pictures of damaged PEI sheets.| |

The rest of the build is exactly the same as a normal klicky. Images are mixed as a I grabbed whatever test parts were on my desk to make the images. 
Glue can be used as needed but please ensure it does not interfere with wire contact. 

If you run into issues I am available on the voron discord most times. Feel free to ping me in this channel.  [Help I broke my klicky](https://discord.com/channels/460117602945990666/969563854071799818). Discord name Dustinspeed#6423. 

Please feel free to reach out if you have any issues.

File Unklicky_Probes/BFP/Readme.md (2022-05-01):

# BFP Unklicky

This is a 6x3 unklicky probe. Thanks go to JosAR for all the hard work and testing. 
bfp BFP

# What do I need?

## Bom
| Name | Pieces |
| --- | --- |
| 6x3MM Magnet | 5|
|12 or 14 mm M3 screw| 1|
|18 to 22 AWG wire| <100 mm|

## Printed parts
| Name | Pieces |
| --- | --- |
| BFP_Unklicky_v6.stlt | 1|
|D_pin_v6.stl| 1|

## Build
| Instruction | Image |
| --- | --- |
|1. Ensure the pin and body slide together very well. Sand or clean up any parts that do not slide well. And that a screw in the pin slot can slide up and down correctly.| |  
|2. Insert rear top magnet. Note: needs to be aligned to attract to dock magnet if existing mount is in place. Or if this is a new installation will need to be reversed alignment from the front 2 slots we will do later.| Instructions|
| 3. Strip and wrap the wire around the pin with the starting point being on the D-cut side of the pin. Multiple wraps around the pin can be used for thinner wires. But you want to be careful to have it flat on the bottom. And use a single twist and cut any extra off on the side as wire binding will cause the pin to not move smoothly.|Instructions Instructions|
|4. Place a magnet on top of the installed rear magnet. And use that to insert the pin mag into the pin. This magnet will be pushed not pulled. So it is not critical to be super secure. For that reason the fit is fairly loose and you may need to slide it off the top. This is by design to prevent any swelling in the pin that can cause roughness in the pin sliding.|Instructions|
|5. Slot the other end of the wire for the pin through the body to the top of the body. Note: in the newer body this will be easier to see and slot. But it is very similar to threading a needle.  Cut and strip the wire on on top with the stripped end going under either magnet.| NOTE: In the image I am showing the path to thread the wire through the part. Instructions|
|6. Slot a new wire for the contact screw strip a small portion of wire. This can either be stuck into the hole and insert the wire or wrap the wire around the screw. On top strip the other side of wire and place under the other front magnet.| NOTE: In the image I am showing the path to thread the wire through the part. Instructions Instructions
|7. Screw the contact screw into place. Ensure that the pin is pushed in and aligned correctly. And that the pin is sliding as expected.| Instructions|
|8. Change the z height for Probe and QGL/z-tilt to a move height of 25 mm. This should work for any of the unklicky probes.| |
|9. While I am not going to go into auto z here. The unklicky currently can start with a switch offset of 6 mm and BFP 3 mm. These should set you a touch high and can be adjusted down. The main variability here is the wire wrap height. But this should be safe for almost anybody. PLEASE test I do not want to see pictures of damaged PEI sheets.| |

The rest of the build is exactly the same as a normal klicky. Images are mixed as a I grabbed whatever test parts were on my desk to make the images. 
Glue can be used as needed but please ensure it does not interfere with wire contact. 

If you run into issues I am available on the voron discord most times. Feel free to ping me in this channel.  [Help I broke my klicky](https://discord.com/channels/460117602945990666/969563854071799818). Discord name Dustinspeed#6423. 

Please feel free to reach out if you have any issues.

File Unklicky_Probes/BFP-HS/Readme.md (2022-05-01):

# BFP-HS Unklicky

This is a 6x3 unklicky probe. Based on the BFP But uses a heat set as the contact point. This allows a shorter throw that is more dialed in. 
BFP-HS
BFP-HS

# What do I need?

## Bom
| Name | Pieces |
| --- | --- |
| 6x3MM Magnet | 5|
|12 or 14 mm M3 screw| 1|
|18 to 22 AWG wire| <100 mm|
|m3 heat set | 1|
|m3 button head x 3 | 1| 

## Printed parts
| Name | Pieces |
| --- | --- |
| BFP-HS.stl | 1|
|Heatset pin_v1.stl| 1|

## Build
| Instruction | Image |
| --- | --- |
|1. Ensure the pin and body slide together very well. Sand or clean up any parts that do not slide well. And that a screw in the pin slot can slide up and down correctly.| |  
|2. Insert rear top magnet. Note: needs to be aligned to attract to dock magnet if existing mount is in place. Or if this is a new installation will need to be reversed alignment from the front 2 slots we will do later.|Instructions|
|3. Use a iron to press the heat set into the end of the pin. Being very careful to stay away from the mag retaining walls. There is a bump added to the model I can feel the heatset when it hits these stops but it possible to push past these stops. So you want a almost hairline amount of heat set showing in the screw slot. Also since we are pressing this through plastic use a pick or file to ensure the botton of the heatset is clear of plastic to make a good connection.|InstructionsInstructions|
|4. Strip and wrap the wire around the m3 screw with sticking out on the D-cut side of the pin.|Instructions|
|5. Place a magnet on top of the installed rear magnet. And use that to insert the pin mag into the pin. This magnet will be pushed not pulled. So it is not critical to be super secure. For that reason the fit is fairly loose and you may need to slide it off the top. This is by design to prevent any swelling in the pin that can cause roughness in the pin sliding.|Instructions|
|6. Slot the other end of the wire for the pin through the body to the top of the body. Note: in the newer body this will be easier to see and slot. But it is very similar to threading a needle. Cut and strip the wire on top with the stripped end going under either magnet.| NOTE: In the image I am showing the path to thread the wire through the part. Instructions|
|7. Slot a new wire for the contact screw strip a small portion of wire. This can either be stuck into the hole and insert the wire or wrap the wire around the screw. On top strip the other side of wire and place under the other front magnet.| NOTE: In the image I am showing the path to thread the wire through the part.Instructions Instructions|
|8. Screw the contact screw into place. Ensure that the pin is pushed in and aligned correctly. And that the pin is sliding as expected.| Instructions|
|9. Change the z height for Probe and QGL/z-tilt to a move height of 25 mm. This should work for any of the unklicky probes.| |
|10. While I am not going to go into auto z here. The unklicky currently can start with a switch offset of 6 mm and BFP 3 mm. These should set you a touch high and can be adjusted down. The main variability here is the wire wrap height. But this should be safe for almost anybody. PLEASE test I do not want to see pictures of damaged PEI sheets. | |

The rest of the build is exactly the same as a normal klicky. Images are mixed as a I grabbed whatever test parts were on my desk to make the images. 
Glue can be used as needed but please ensure it does not interfere with wire contact. 

If you run into issues I am available on the voron discord most times. Feel free to ping me in this channel.  [Help I broke my klicky](https://discord.com/channels/460117602945990666/969563854071799818). Discord name Dustinspeed#6423. 

Please feel free to reach out if you have any issues.

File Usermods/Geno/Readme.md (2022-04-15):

lets you use a m3x20mm screw and holds it nicely.

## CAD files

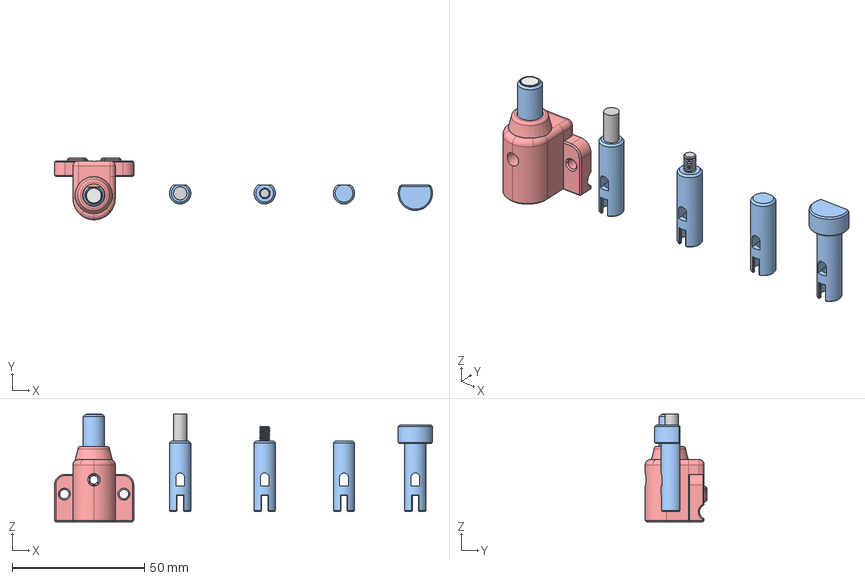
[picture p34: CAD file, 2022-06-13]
Unklicky_Endstops/Unklicky_z/CAD/unklicky z heatset_v4.step
143.1 x 23.3 x 40.8 mm
Unklicky_z
Magnet Lower pin
Pin screw
Heatset (1)
Bottom mag
Contact Mag
Contact Heatset x 2
Z_Pin
Z_Pin 5mm pin
Z_Pin m4 threaded
Z_Pin Blank big
Z_Pin blank
Unklicky_Sexbolt
Contact Screw

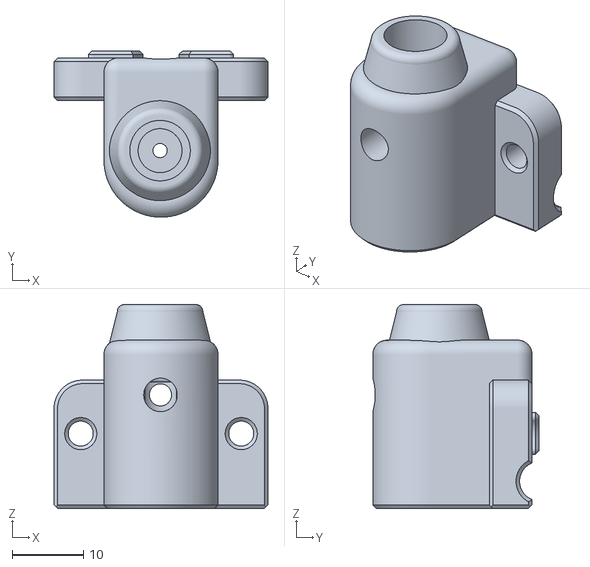
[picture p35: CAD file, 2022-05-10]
Unklicky_Endstops/Unklicky_z/STL's/Unklicky_z_v4_body.stl
30.0 x 23.3 x 28.6

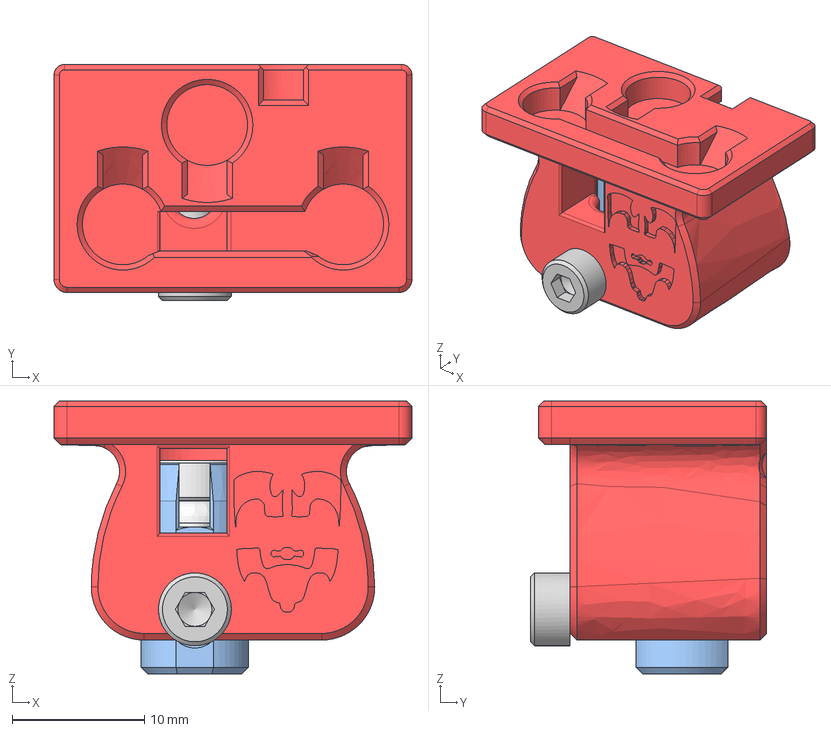
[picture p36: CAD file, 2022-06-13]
Unklicky_Probes/BFP-HS/CAD/BFP-HS_Unklicky_Probe v8.step
27.0 x 17.8 x 20.6 mm
Thicc Unklicky
Pin
Pin Magnet
M3x16 SHCS
BFP-HS
Magnet pin
Heatset pin
BFP HS pin
M3 x 5 BH

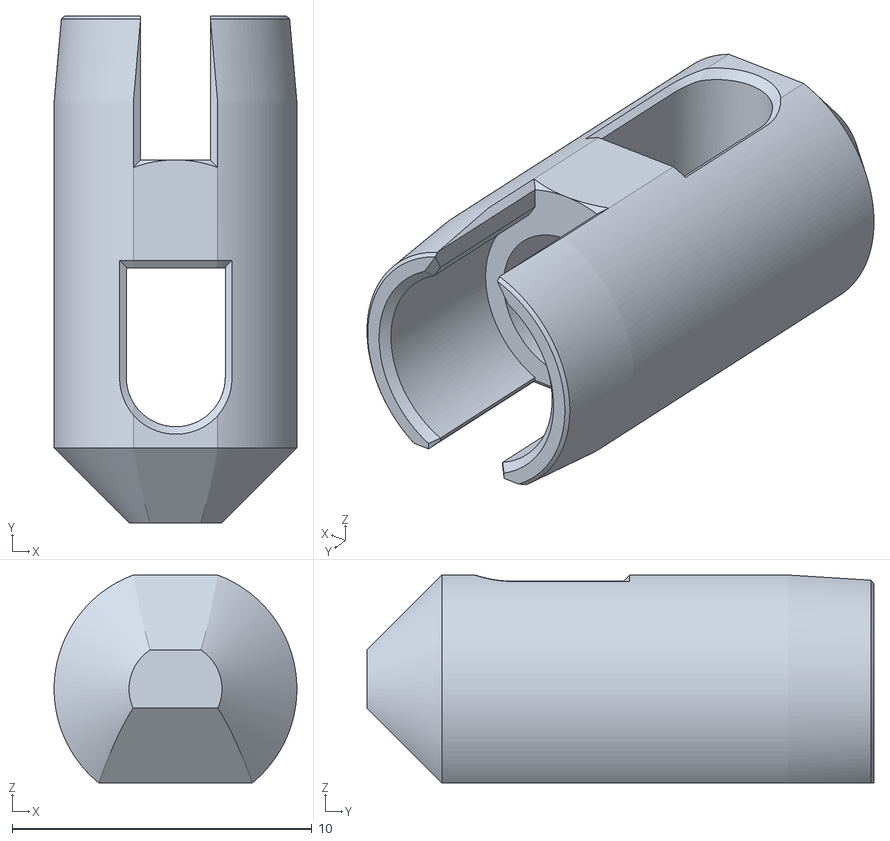
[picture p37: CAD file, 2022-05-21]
Unklicky_Probes/BFP-HS/STL/BFP HS pin Sharp.stl
8.10 x 16.9 x 6.94

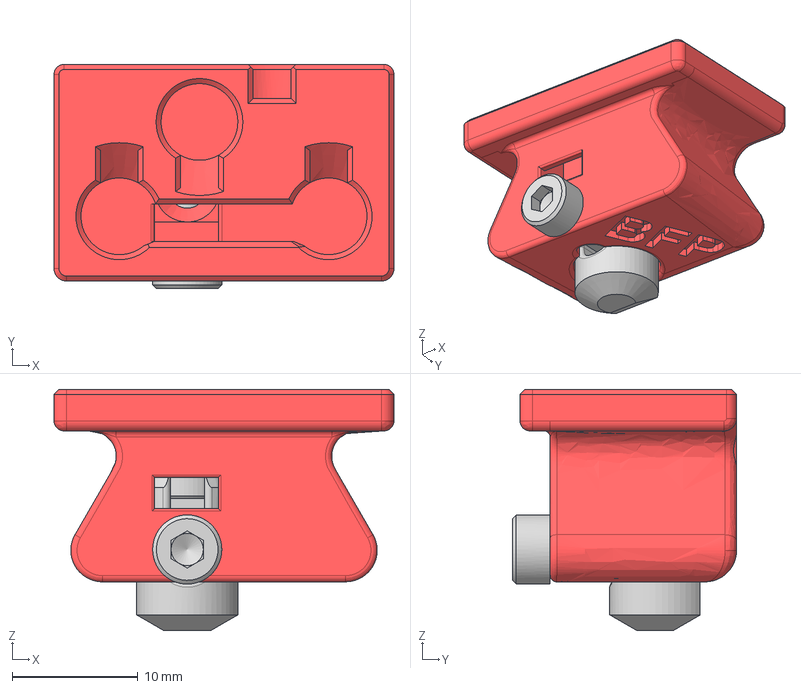
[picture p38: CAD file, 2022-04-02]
Unklicky_Probes/BFP/CAD/BFP_Unklicky_Probe v6.step
27.0 x 17.8 x 19.2 mm
Thicc Unklicky
Pin
Pin Magnet
M3x16 SHCS

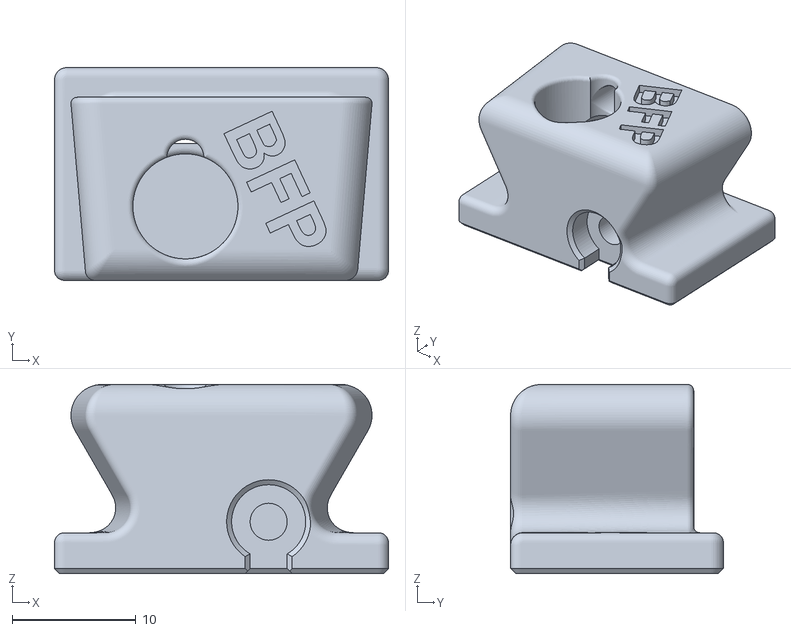
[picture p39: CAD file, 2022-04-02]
Unklicky_Probes/BFP/STL/BFP_Unklicky_v6.stl
27.0 x 17.2 x 15.3

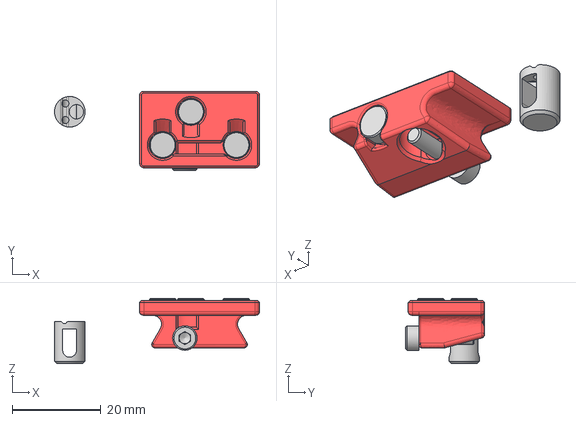
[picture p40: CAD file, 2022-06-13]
Unklicky_Probes/Unklicky/CAD/Unklicky_shaped_pin.step
46.2 x 17.8 x 14.7 mm
Unklicky
M3x16 SHCS

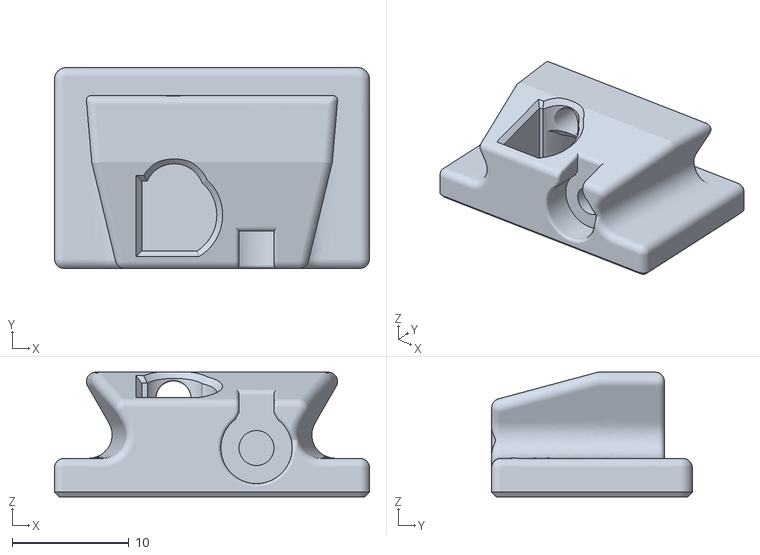
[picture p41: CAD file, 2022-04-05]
Unklicky_Probes/Unklicky/STL/Unklicky_Shapedpin_body_v2.stl
27.0 x 17.2 x 10.7

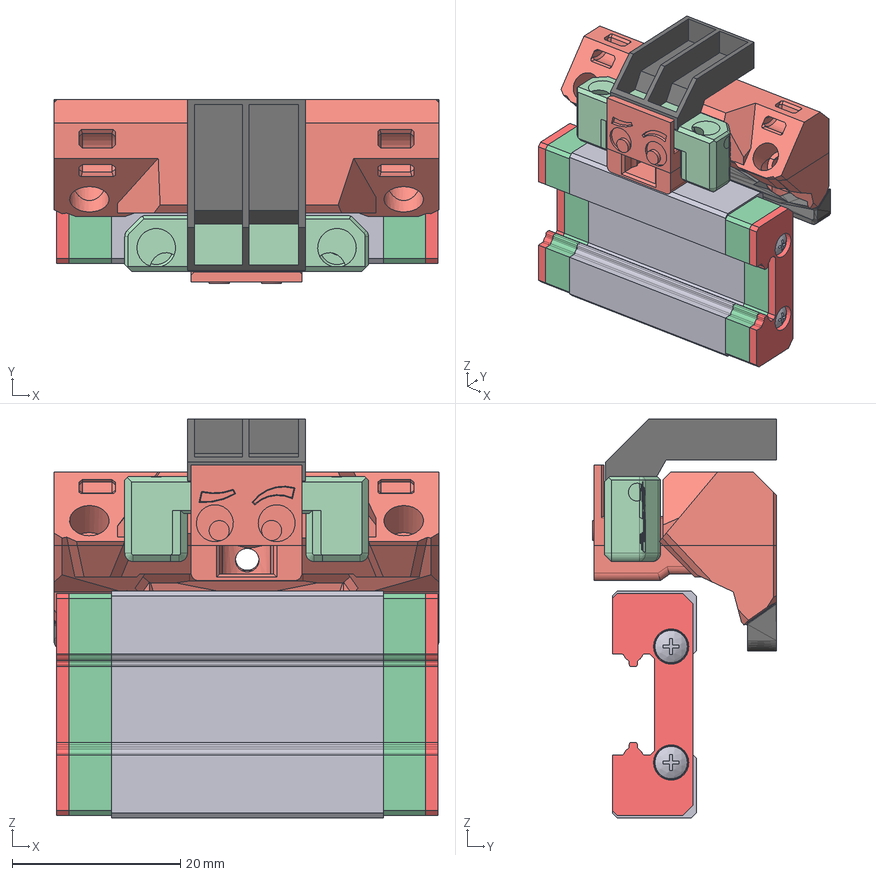
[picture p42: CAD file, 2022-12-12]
Unklicky_TAP/CAD/UnTAP_v7.step
45.8 x 21.9 x 47.5 mm
unTAP_Body
UnTAP_pin
PRODUCT_NAME_1
PRODUCT_NAME_6
PRODUCT_NAME_5
PRODUCT_NAME_7
PRODUCT_NAME_4
PRODUCT_NAME_8
PRODUCT_NAME_3
PRODUCT_NAME_2
PRODUCT_NAME_9

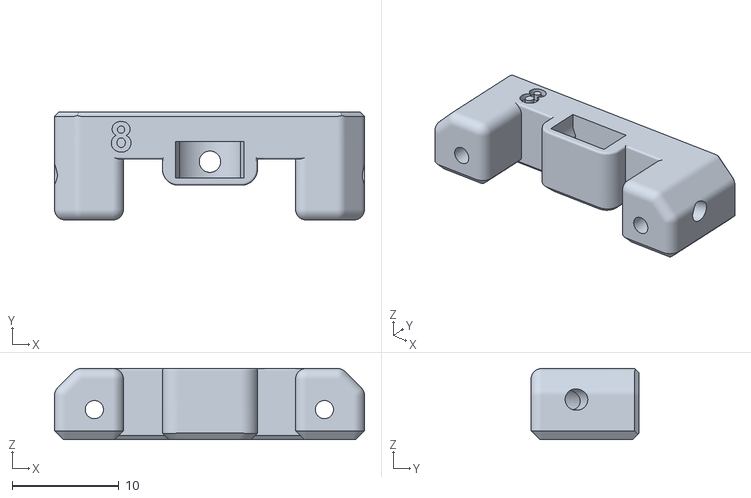
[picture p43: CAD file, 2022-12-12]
Unklicky_TAP/STL/UnTAP_pin_8mm_v3.stl
29.0 x 10.1 x 6.65

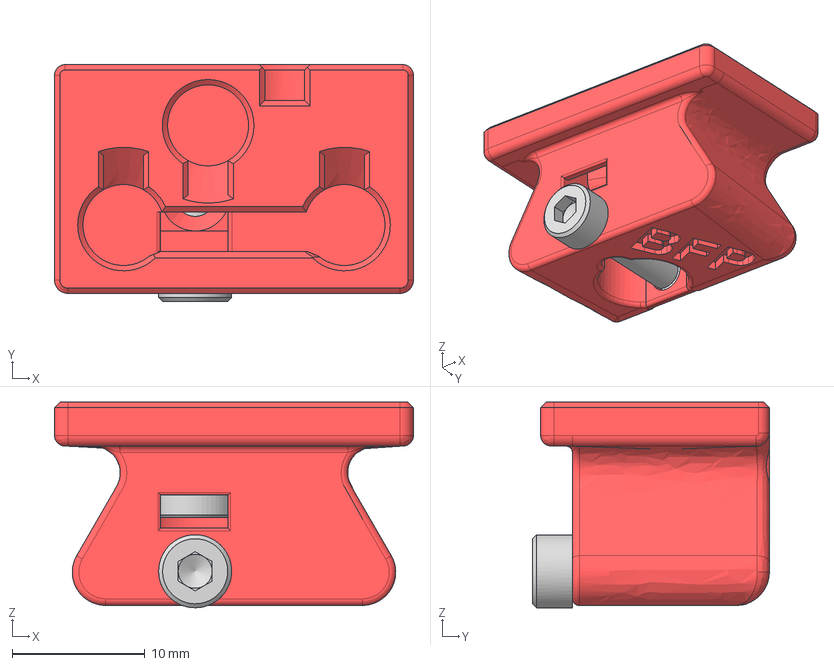
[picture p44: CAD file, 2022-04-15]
Usermods/Geno/CAD/BFP_Unklicky_Probe_vGeno.step
27.0 x 17.8 x 15.5 mm
Thicc Unklicky
Pin Magnet
M3x16 SHCS

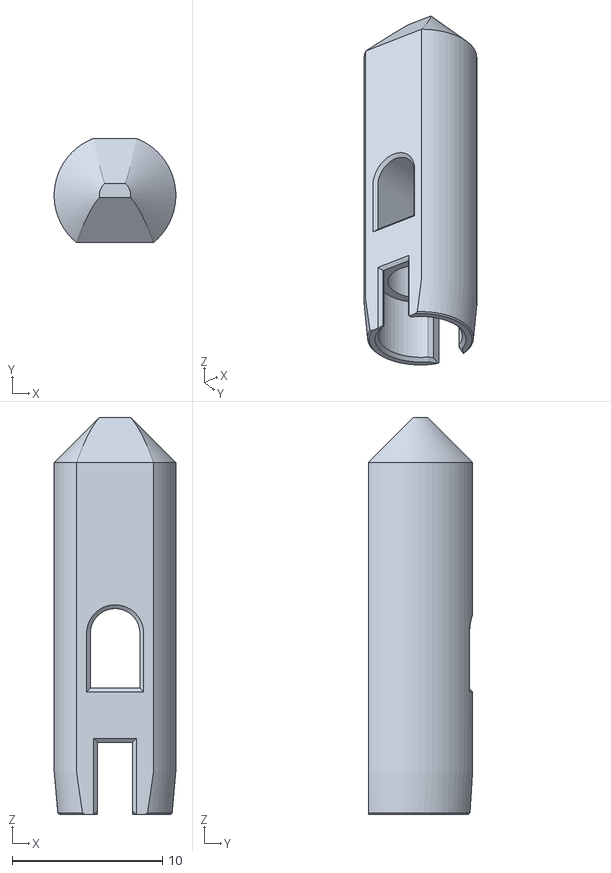
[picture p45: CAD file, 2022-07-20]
Usermods/Mantis Volcano/STL/PIN.stl
8.09 x 6.94 x 26.4

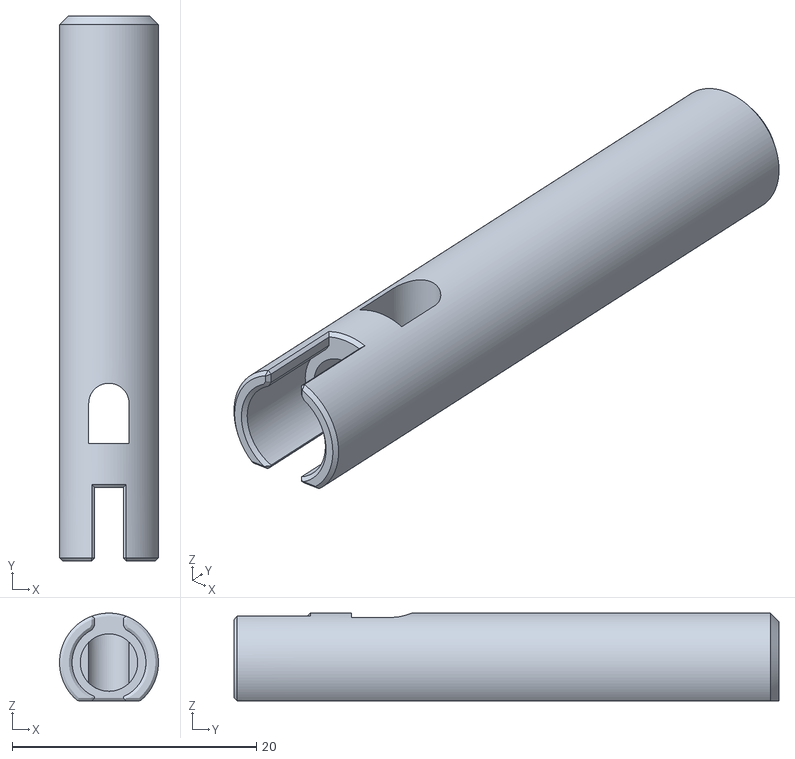
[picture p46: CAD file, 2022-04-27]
Unklicky_Endstops/Unklicky_z/STL's/Kinematic_Z_Pin.stl
8.10 x 44.6 x 7.19

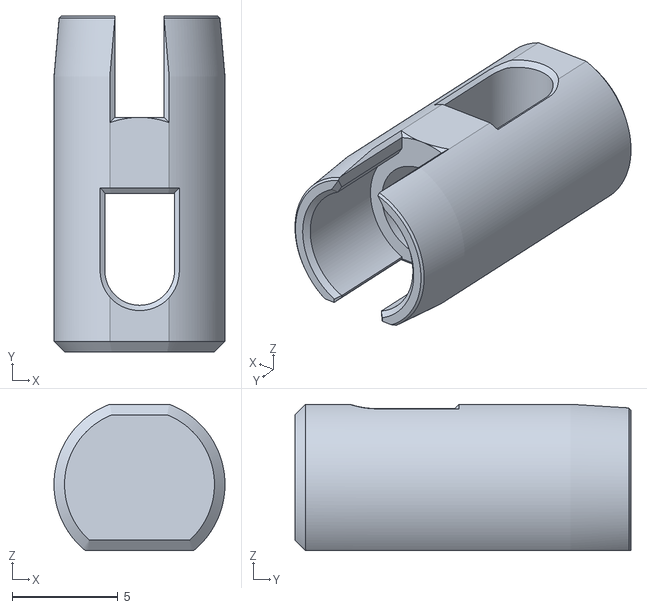
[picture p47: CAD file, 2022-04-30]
Unklicky_Probes/BFP-HS/STL/Heatset pin_v1.stl
8.10 x 15.9 x 6.94

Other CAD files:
Usermods/Geno/STL/Geno_BFP_SN.stl
Unklicky_Probes/BFP/STL/D_pin_v6.stl
Unklicky_Probes/Unklicky/STL/Shapedpin_point_v2.stl
Unklicky_TAP/STL/UnTAP_pin_12mm_v3.stl
Unklicky_Endstops/Unklicky_SexBolt/CAD/UnKlicky_SexBolt M6.step
Unklicky_Endstops/Unklicky_SexBolt/CAD/UnKlicky_SexBolt_bearing_v2.step
Unklicky_Endstops/Unklicky_SexBolt/STL's/Unklicky_SBS_Body.stl
Unklicky_Endstops/Unklicky_SexBolt/STL's/Unklicky_SBS_bottom.stl
Unklicky_Endstops/Unklicky_SexBolt/STL's/Unklicky_SB_Body_6mm.stl
Unklicky_Endstops/Unklicky_SexBolt/STL's/Unklicky_SB_Body_v2.stl
Unklicky_Endstops/Unklicky_SexBolt/STL's/Unklicky_SB_bottom_6mm.stl
Unklicky_Endstops/Unklicky_SexBolt/STL's/Unklicky_SB_pin.stl
Unklicky_Endstops/Unklicky_SexBolt/STL's/Unklicky_z_6mm_pin.stl
Unklicky_Endstops/Unklicky_z/STL's/Kinematic_Z_Pin 5mm pin.stl
Unklicky_Endstops/Unklicky_z/STL's/Kinematic_Z_Pin m4 threaded.stl
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

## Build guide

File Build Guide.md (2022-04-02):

# The build 

While this written with the BFP as an example. Essentially the same steps are used for both probes. 

Gather Up all the materials. Test fit the pin ensure it is not binding or to tight. it should slide easily in and out without binding. 
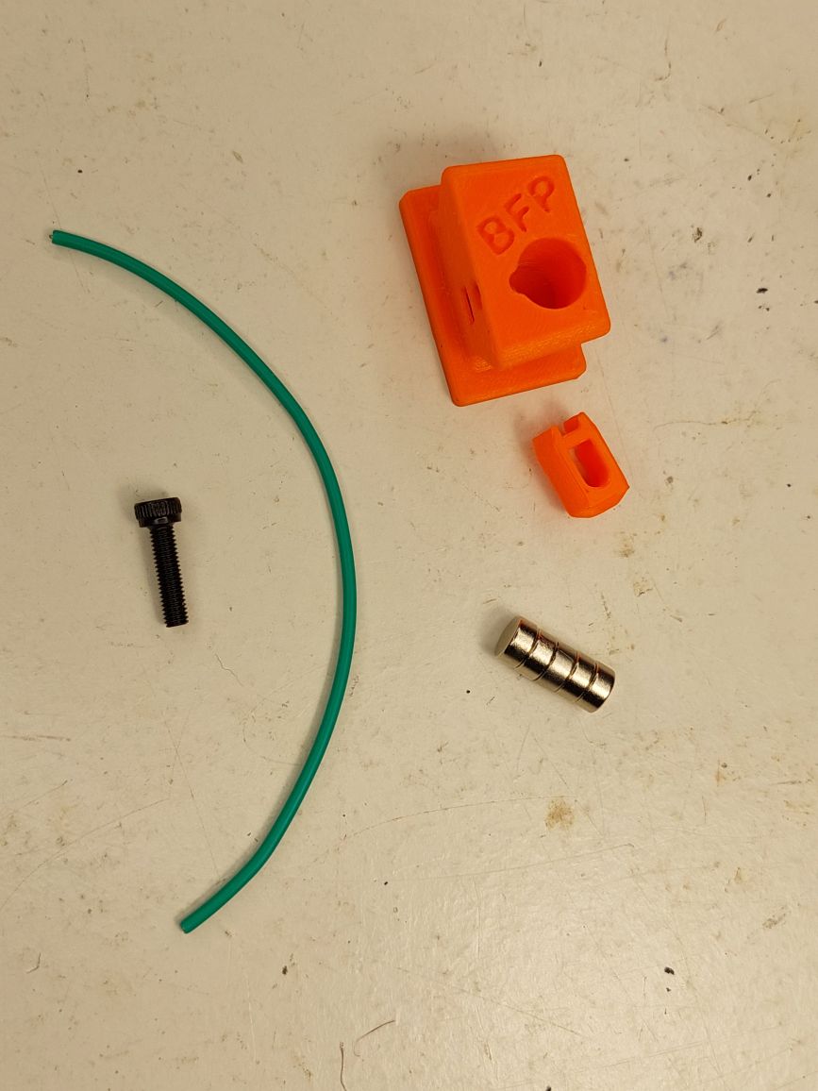
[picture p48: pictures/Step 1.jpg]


## The Pin

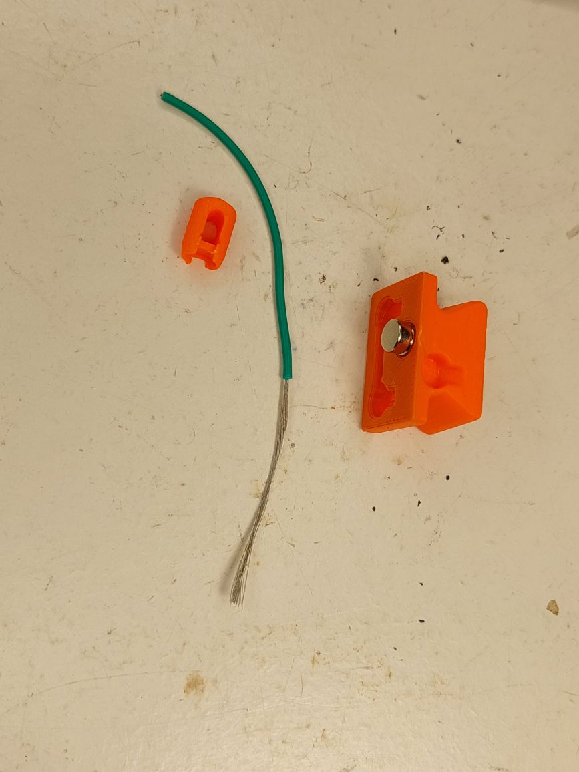
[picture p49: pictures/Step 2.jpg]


Strip a length of wire and thread through the hole in the pin. 

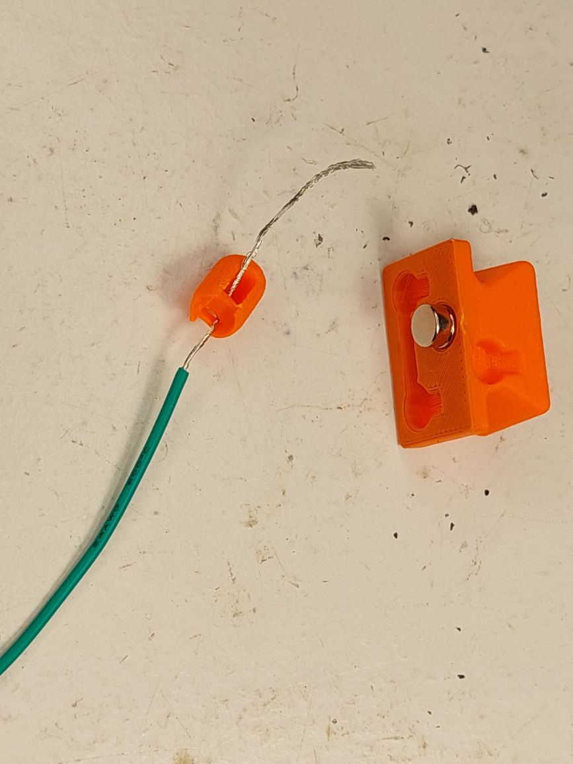
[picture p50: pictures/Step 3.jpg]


Flip the wire over towards the opposite side of the pin, the back of the D shape must be facing the back of the probe when assembled.

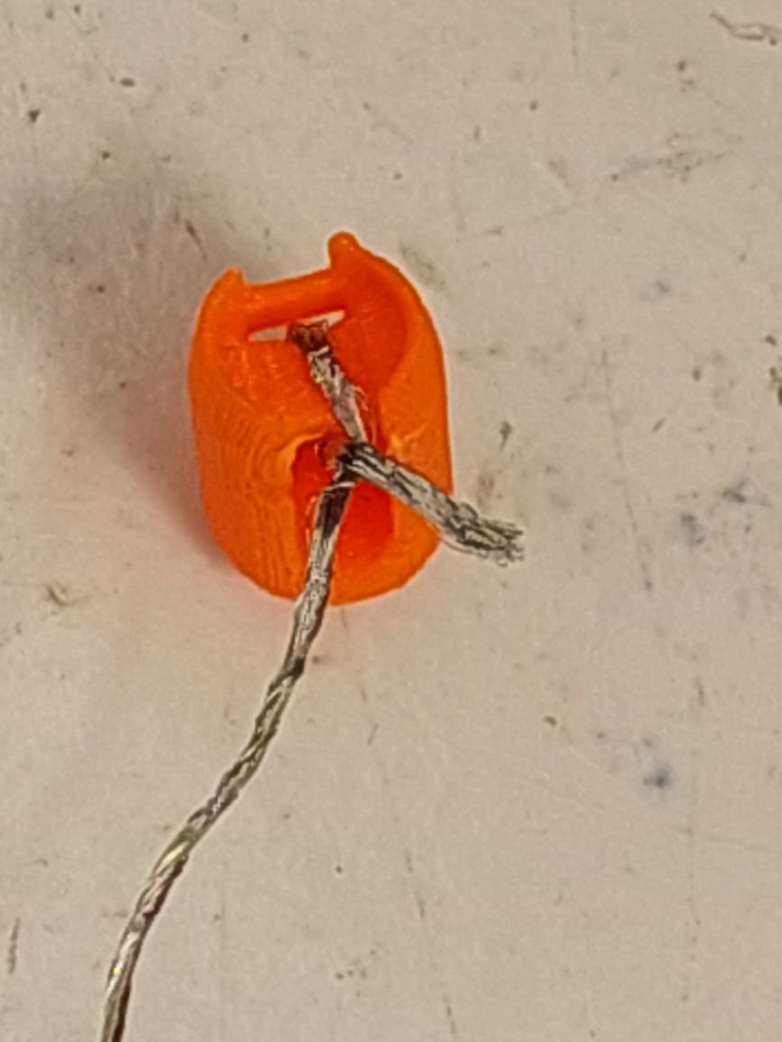
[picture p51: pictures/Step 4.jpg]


You want a single twist of wire. NOT TO MUCH this will cause issues if you leave to much here. Trim the excess. 
Twist the two wires well , so that they are straight on the bottom part that will touch the screw.

If you have issues with the fit you can strip the wire completely bare (it slides much better that way). 

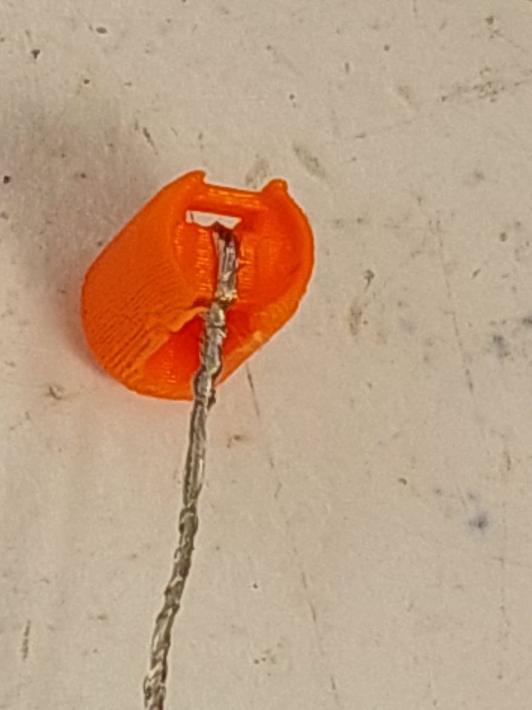
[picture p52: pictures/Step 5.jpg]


Insert the magnet in the top of the pin. Ensure that the magnet will be repelled buy the magnet on top, use the image below as reference.
This does not need to be crunched down. It is not designed to be tight. 
If you have issues with it slipping use a drop of glue.
There does not need to be contact between the wire and the magnet. But contact will not hurt it either. 

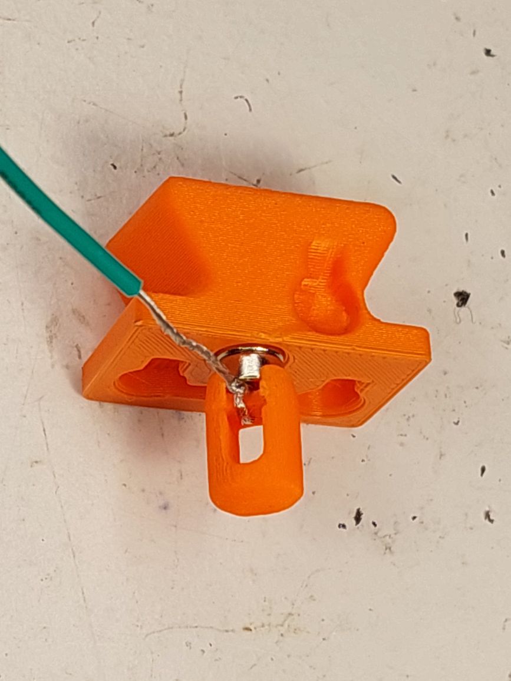
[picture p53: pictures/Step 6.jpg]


Run the wire up the hole a tiny bend at the end may be useful. 

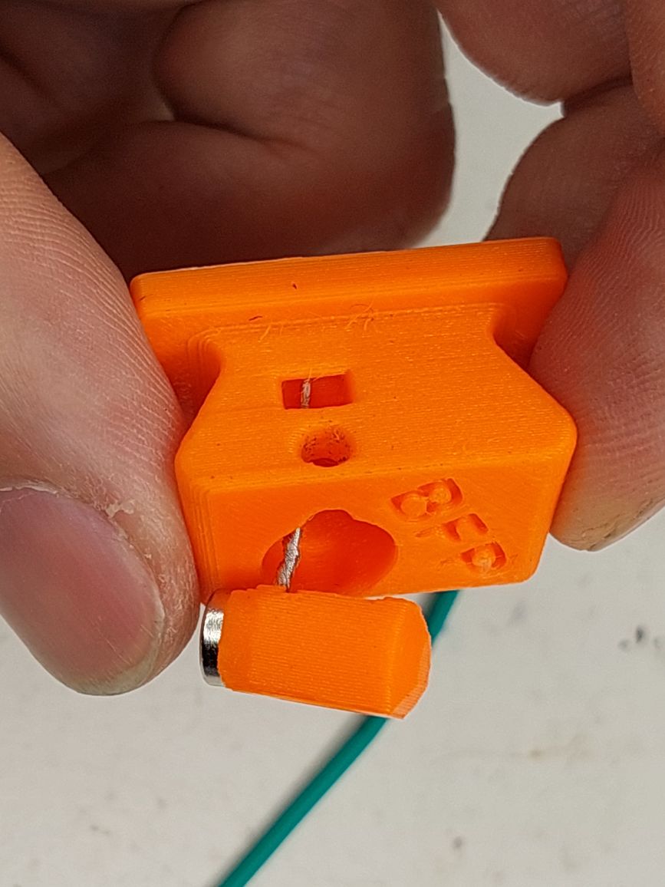
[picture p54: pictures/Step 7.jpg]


Pull the wire as you continue to insert it until it is fully seated.

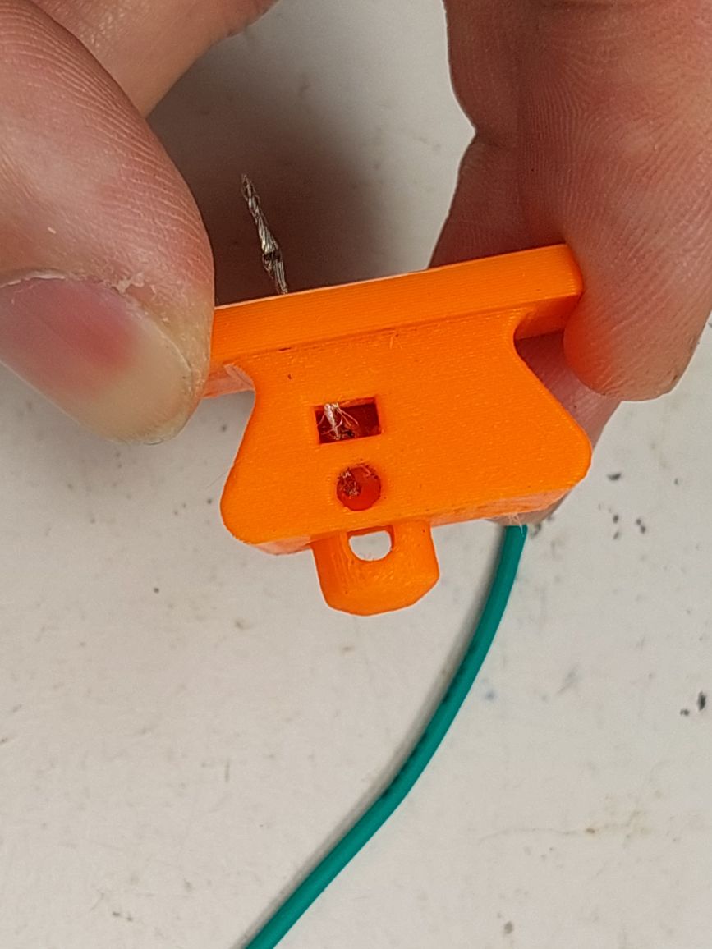
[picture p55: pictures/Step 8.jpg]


Finally strip the end if it is not bare and lay under the magnet and insert your magnet. 

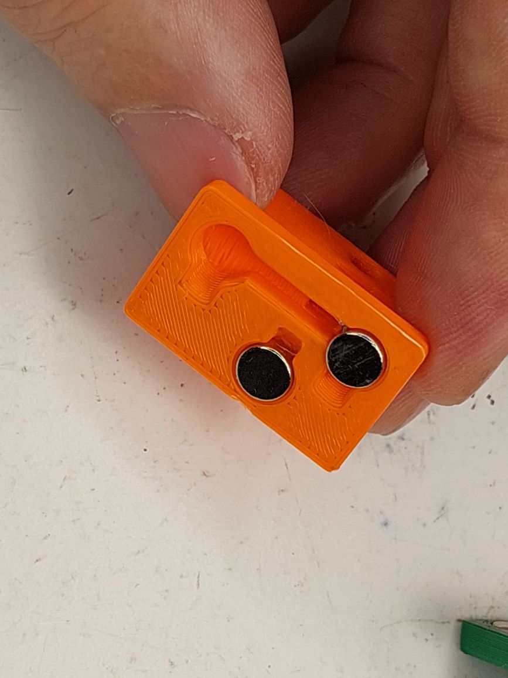
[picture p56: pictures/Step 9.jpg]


# Contact Screw
Strip a piece of wire and thread from the top down and out the front of the body. 
This piece of wire cannot be bare. 

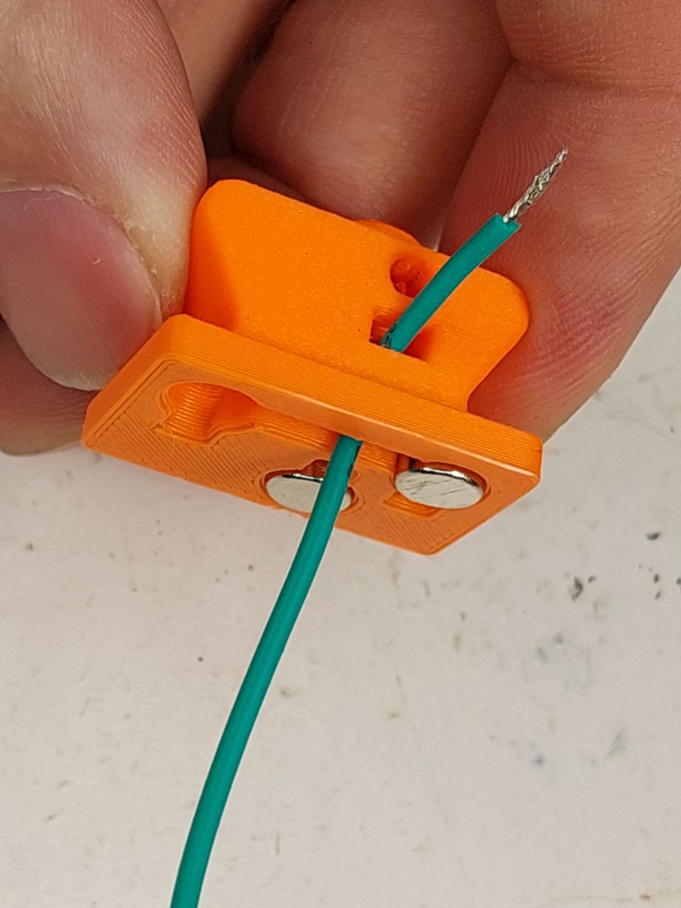
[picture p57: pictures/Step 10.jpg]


slot the wire into the screw hole on the front of the body.

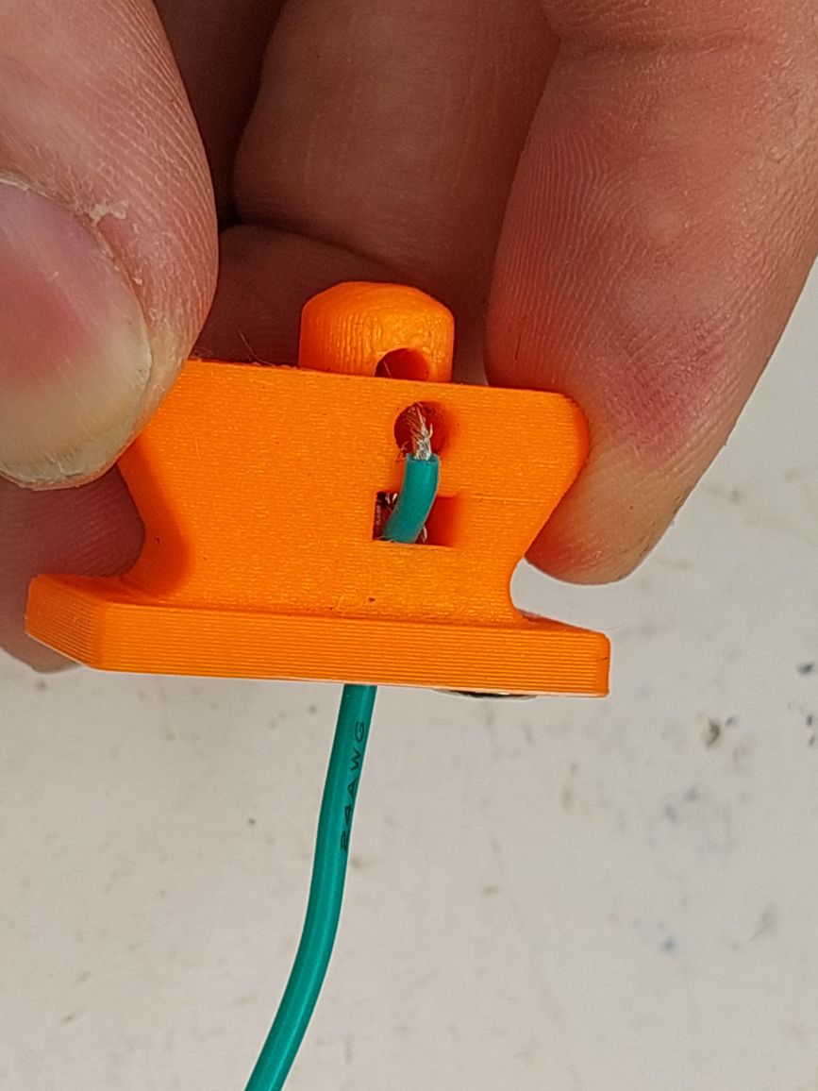
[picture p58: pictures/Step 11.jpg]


start the srew into the hole. 

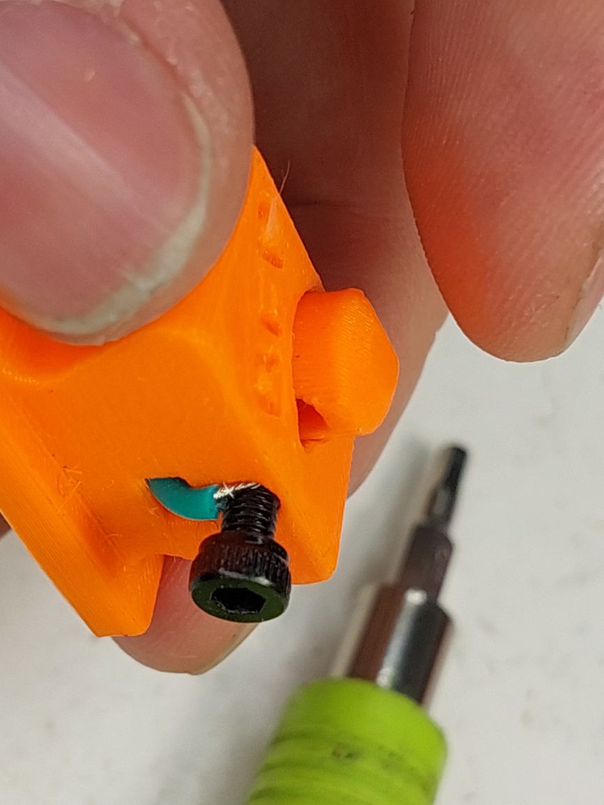
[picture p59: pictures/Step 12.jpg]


cut and strip the wire on the top to sit under the second magnet on top. 

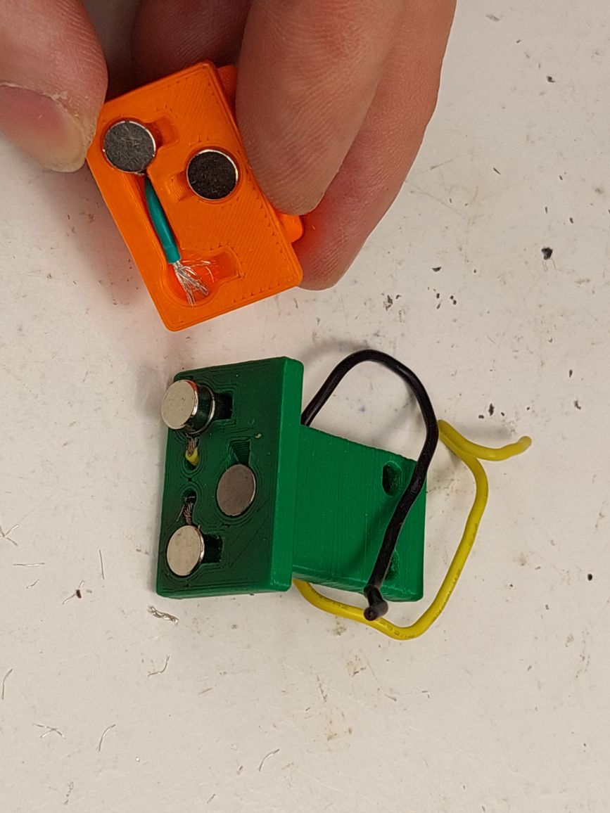
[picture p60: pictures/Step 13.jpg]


Press the magnet down on top. And finish screwing the contact screw all the way in. 

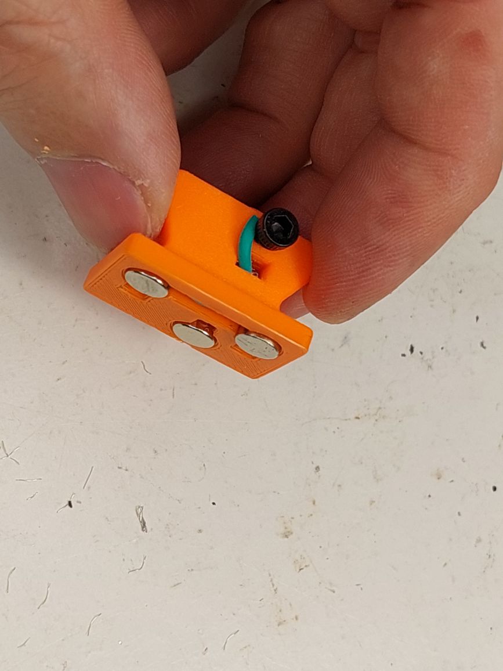
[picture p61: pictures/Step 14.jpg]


Press in the rear magnet and enjoy your self built switch. 

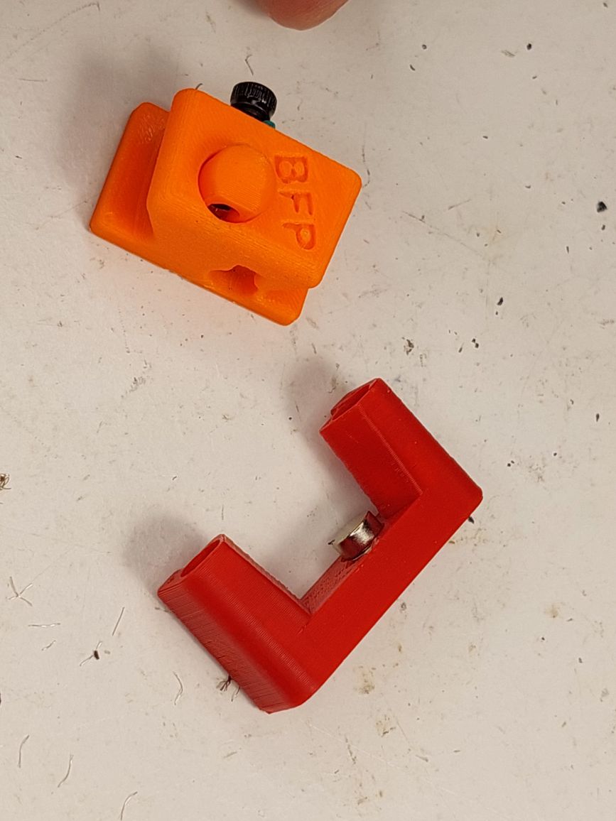
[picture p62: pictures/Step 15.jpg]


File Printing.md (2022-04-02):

# Printing 
There is only one thing. I have found so far is that the wire holes have to be so close to the edge. You need to turn on overlapping perimeter in susperslicer to keep the top together. 

Overlapping
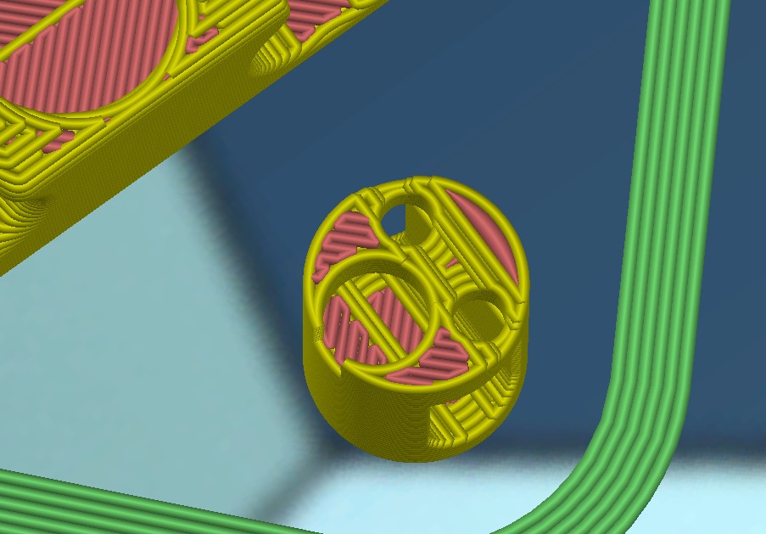
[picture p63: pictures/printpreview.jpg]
Printpreview Preview


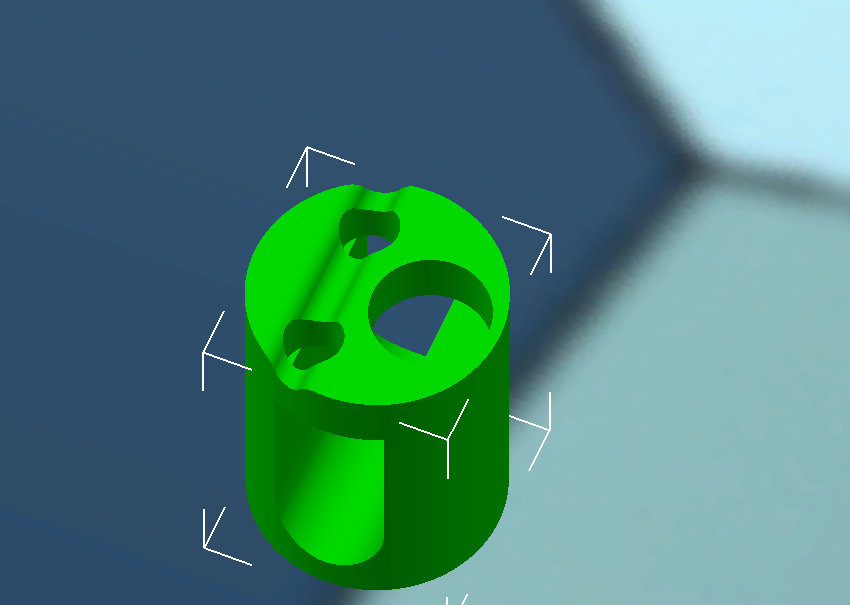
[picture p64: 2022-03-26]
pictures/Printstalk.png

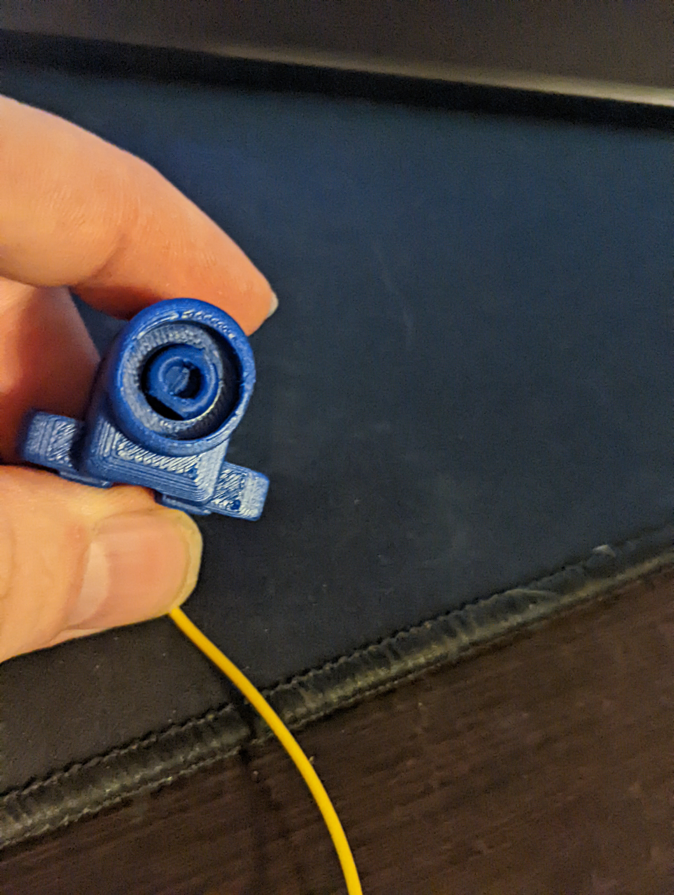
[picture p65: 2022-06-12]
pictures/SB_step2_2.jpg

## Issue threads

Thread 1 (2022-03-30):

Stalk Alignment

0x3333, 2022-03-30:
Is it normal to the stalk be miss aligned?

It’s the effect of the repulsing magnet is not aligned.

Is this expected ?

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

Edit: it work as expected, like a spring. But I don’t know if it is supposed to be this way.

majarspeed, 2022-03-30:
there should be a tight enough fit on the screw to keep it straight. I have created some tighter tolerance pins and waiting for feedback.

0x3333, 2022-03-30:
I tried the -0.1 and -0.2 same situation, just a little better.

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

What is the supposed orientation of the small magnet? Near the center or the border?

majarspeed, 2022-03-30:
Small magnet should be to the inside.

0x3333, 2022-04-01:
Well, looks like the missing magnets have an effect aligning the stalk.

Closed 2022-04-01.

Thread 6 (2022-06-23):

Corrupted STEP files?

TheHumbleOne1, 2022-06-23:
I cant open STEP files for BFP and also Unklicky/Unklicky_Probes/Unklicky/CAD/
I suspect files might be corrupted? I am using F360.
I also can't open them with "online step viewers".

jlas1, 2022-07-08:
Hello, i checked the files, i can open them, and you can check that github STL viewer also can display them.
Maybe they are getting corrupted when you save them?

TheHumbleOne1, 2022-07-08:
Hi, I just checked again. If I right clicked and saved file, it didn't work. But when I opened stl preview and downloaded or saved "raw" step, it worked as it should. Thank you again for helping me and thank you sir for releasing this project, I'm grateful.

jlas1, 2022-07-08:
it's mostly @majarspeed project, i am just helping along :-) but thanks.

Closed 2022-07-08.

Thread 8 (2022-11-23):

how to assemble Unklicky v2?

thijsdeschildre, 2022-11-23:
The photos don't match the STL. I don't understand how to wrap the wire on Shapedpin_point_v2.stl

Closed 2023-12-28.

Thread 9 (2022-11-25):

how to assemble BFP-HS Unklicky ?

thijsdeschildre, 2022-11-25:
I can't figure out how to run the wire through the part, I can't make sense from the photos and the description.
Also, he photos don't match the STL's.  I think the threaded insert has to be set deeper than the photo indicates?
Is the threaded insert M3x5x4 ?

Closed 2023-12-28.

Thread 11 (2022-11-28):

Support on the "slim" version to thin

Exerqtor, 2022-11-28:
Just printed the "slim" version, and it came out great except that the chamfer on the supported partion is overhaning the built-in support to much. Leaving a less than ideal result 😅

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

I've widened the support with 1mm in total so that it's fully supporting everything:
https://mega.nz/folder/sV8TGSID#w6U6yWF4Cdu5oPiOOKkUmg

jlas1, 2022-11-28:
Solved, thanks

Closed 2022-11-28.

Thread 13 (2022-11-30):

Non standard MGN12H carriage

ManiekJG, 2022-11-30:
I would love to switch to VORON TAP using Unklicky as I can't get a hold of optical sensor. However I have an issue with my linear rail carriage. I have a RobotDigg MGN12H which has plastik / non conductive part where the screws are supposed to make contact (half of carriage thickness). Would there be any chance for a version for these kinds of carriage?

0x3333, 2023-05-18:
Just add an Adhesive Conductive Tape to it.

[Like this](https://www.aliexpress.com/item/1005003118020966.html)

majarspeed, 2023-12-28:
No redesign planned right now.

Closed 2023-12-28.

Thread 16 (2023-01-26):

Probe samples exceed samples tolerance

laserbeak, 2023-01-26:
Hi,
Just got Unklicky Tap running, but I can't get consistent measurements.

```
05:18:07 // Klipper state: Ready
05:18:29 $ G28
05:19:12 // probe at 50.000,25.000 is z=6.603000
05:19:13 // probe at 50.000,25.000 is z=6.635500
05:19:13 // Probe samples exceed tolerance. Retrying...
05:19:13 // probe at 50.000,25.000 is z=6.648000
05:19:14 // probe at 50.000,25.000 is z=6.635500
05:19:14 // Probe samples exceed tolerance. Retrying...
05:19:15 // probe at 50.000,25.000 is z=6.618000
05:19:16 // probe at 50.000,25.000 is z=6.655500
05:19:16 // Probe samples exceed tolerance. Retrying...
05:19:17 // probe at 50.000,25.000 is z=6.635500
05:19:17 // probe at 50.000,25.000 is z=6.633000
05:19:18 // probe at 50.000,25.000 is z=6.660500
05:19:18 !! Probe samples exceed samples_tolerance
```
My probe from printer.cfg:
```
[probe]
pin: ^PG15
x_offset: 0
y_offset: 0
speed: 5.0
samples: 3
samples_result: median
sample_retract_dist: 1.0

samples_tolerance: 0.01
samples_tolerance_retries: 3
```

Not sure why it's so inaccurate

erlis, 2023-05-20:
Hi @laserbeak

These are my settings, I see that my samples_tolerances are a bit higher than yours, try with my values and see if it works. I also increased the samples from 3 to 5.

These settings have been working great for me!

```
[probe]
##	Inductive Probe - If you use this section , please comment the [bltouch] section
##	This probe is not used for Z height, only Quad Gantry Leveling
##	In Z+ position
##	If your probe is NC instead of NO, add change pin to ^PA3
#pin:  ^PA3
pin: ^can0:LIMIT_1
x_offset: 0
y_offset: 0   # changed because of TAP
#z_offset: 6.42
speed: 5
samples: 5
sample_retract_dist: 1.0
samples_tolerance: 0.05
samples_tolerance_retries: 5

samples_result: median
#sample_retract_dist: 3.0
#samples_tolerance: 0.006
#samples_tolerance_retries: 3

# TAP Active GCODE
activate_gcode:
    {% set PROBE_TEMP = 150 %}
    {% set MAX_TEMP = PROBE_TEMP + 5 %}
    {% set ACTUAL_TEMP = printer.extruder.temperature %}
    {% set TARGET_TEMP = printer.extruder.target %}

    {% if TARGET_TEMP > PROBE_TEMP %}
        { action_respond_info('Extruder temperature target of %.1fC is too high, lowering to %.1fC' % (TARGET_TEMP, PROBE_TEMP)) }
        M109 S{ PROBE_TEMP }
    {% else %}
        # Temperature target is already low enough, but nozzle may still be too hot.
        {% if ACTUAL_TEMP > MAX_TEMP %}
            { action_respond_info('Extruder temperature %.1fC is still too high, waiting until below %.1fC' % (ACTUAL_TEMP, MAX_TEMP)) }
            TEMPERATURE_WAIT SENSOR=extruder MAXIMUM={ MAX_TEMP }
        {% endif %}
    {% endif %}
```

davinche, 2023-06-16:
I actually had a lot of issues at first as well. After much experimentation, it turns out that the M3x6 FHSC screws I used (the ones that are used in the carriage in conjunction with magnets to position the printhead back into place) were not "metalic" enough. This lead to the printhead not moving back into position in between taps.

Once i swapped out the screws for more "metalic" ones, the difference was night and day.

majarspeed, 2023-12-28:
Thanks for letting us know.

Closed 2023-12-28.

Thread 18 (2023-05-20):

Implement Tap R8 changes to the body!

erlis, 2023-05-20:
With the new version of Tap R8 we have some improvements and one was moving the hole on the top part 0.4mm as shown in the image.

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

It would be nice if we can implement the same change here, I'm using the xol2 toolhead and changes are being made to the Tap Version to align with R8.

I hope this gets some attention here and thanks for providing with this awesome alternative, it has been working awesome for me!

buhralex, 2024-03-08:
From the picture I cannot exactly make out the hole that needs to be edited.
I think it might be the holes where the headset inserts are going in?
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

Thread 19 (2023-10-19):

Proposal: SexPillar

PorcoMaster, 2023-10-19:
Hi, so... i am a little out of my element here, first time doing anything on github,

i just finished a fully parametric design of a new endstop, and i would love to be mentioned on your project, it's made with same idea of always closed and magnets as unklicky, but it's fully parametric, for printers that are bedslingers and normally have electronics in the bottom and metal bottom. as it uses a magnet to make it firm in base

this is the project, i would be honored to be mentioned on this project

https://github.com/PorcoMaster/SexPillar

jlas1, 2023-10-21:
Hi, let me check what can be done

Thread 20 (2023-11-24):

Mistake or intendent higher face?

tomdelahaba, 2023-11-24:
Hello, I have to (unfortunately) modify the step for use of 5x3 magnets (6x3 are very hard to buy in here and I do not want to wait for the magnets to arrive from China). So I am about to modify the model, unfortunately I see that one magnet (the top one on the face where these 3 magnets are, so inside one of them, the face is a little bit higher then I would suppose. Is it meant to be like this or is it just some small mistake? That face seems to be extruded towards the top by 0.1mm

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

Another "question" I would have is, the holes for magnets seems to be 2.8mm deep, while magnets are 3mm. Is it mean to be like that so the magnets overflow the top face?

majarspeed, 2023-12-28:
I believe we spoke on discord but yes this is as intended. 2 magnets get wires under them and one does not this is done to attempt to level as best I can when that is done.

Closed 2023-12-28.

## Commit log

2022-04-02 updates
    Step and stl update, minor text revisions
    [BFP Unklicky5.stl, BFP_Unklicky_Probe v6.step, BFP_Unklicky_Probe_v2.step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]
2022-04-25 Add files via upload
    New pin and body
    [unklicky z heatset_v3.step]
2022-04-25 Add files via upload
    New heatset pin and body
    [Unklicky_z.stl, Z_Pin.stl]
2022-06-13 file restructuring
    [BFP HS pin Sharp.stl, BFP-HS.stl, BFP-HS_Unklicky_Probe v8.step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]
2022-06-13 directory names update
    [BFP HS pin Sharp.stl, BFP-HS.stl, BFP-HS_Unklicky_Probe v8.step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]
2022-06-13 more directory names corrections
    [Kinematic_Z_Pin 5mm pin.stl, Kinematic_Z_Pin m4 threaded.stl, Kinematic_Z_Pin.stl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]
2022-07-20 Add unklicky for Mantis and Volcano.
    [PIN.stl, Probe.stl.stl]
2022-07-20 Add files via upload
    Corrected the name
    [Probe.stl]
2022-11-24 added support for a new unklicky sensor
    [Unklicky_TAP_Body.stl, Unklicky_TAP_Body_slim.stl, Unklicky_TAP_pin_10mm.stl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]
2022-11-28 increased pin screw hole size by 0.1mm, small readme fixes
    [Unklicky_TAP_Body_slim.stl, Unklicky_TAP_pin_10mm.stl, Unklicky_TAP_pin_slim_10mm.stl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]
2022-11-29 unklicky TAP discontinued, slim version updated
    [Unklicky_TAP_Body.stl, Unklicky_TAP_Body_slim.stl, Unklicky_TAP_pin_10mm.stl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]
2022-12-01 naming update, 9mm pin and tilted pin added
    [UnTAP_pin_10mm.stl, UnTAP_pin_10mm_RobotDigg.stl, UnTAP_pin_9mm.stl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]
2022-12-05 parts update for better reliability
    [UnTAP_pin_10mm.stl, UnTAP_pin_10mm_RobotDigg.stl, UnTAP_pin_10mm_angled_v2.stl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]
2022-12-12 expanded pin for easier sanding, small tweak on the body
    [UnTAP_Body_v3.stl, UnTAP_pin_10mm_v2.stl, UnTAP_pin_10mm_v3.stl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]
2023-05-18 adds heatset inserts to Unklicky TAP BOM section
    The amount of M3 heatset inserts required for a TAP switch carrier can vary.
    This commit adds the appropriate amount to the Unklicky TAP BOM.
2023-05-18 pin movement check for Unklicky TAP instructions
    The pin needs to be able to move freely in the body part for safe operation.
    This may not be the case if the printed parts have slight deficiencies.
    These can include overextruded top or coarse bottom layers (textured PEI).
    This commit adds a relevant safety check to the build instructions.
    It also provides a tip about sanding pin parts.
